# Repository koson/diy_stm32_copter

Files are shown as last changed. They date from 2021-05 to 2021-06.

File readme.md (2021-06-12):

# About the project
- This is my mini project to design a simple PCB that can be used to control a quad or hexa multicopter Design. 
- Thanks PCB Electronics sub-reddit for consulted me.
- The 'stm_multicopter_gerber_v1.2.rar' was used to make the actual PCB I use in this project. -> The bare PCB board photo 'multicopter_bare_pcb.JPG'
- Other notes (mainly plenty of reference PCB design projects): nguye\OneDrive\technical_workspace\Altium_workspace\altium_stm32_copter_hhh
# The firmware
- After finishing soldering the board, I've made several tests on each designed peripherals, you can find them under 'testfirm' folder.
- A video I made to test the ICM AHRS module: https://www.youtube.com/watch?v=TO57MewXJ6E&ab_channel=Edinhthong
- SDcard module code: https://github.com/dinhthong/stm32f4_sd_logger/
# Connect PCB with debugger
## SWD interface
Pin | #Debugger | #Target | #Note
--- | --- | --- | ---
GND | GND | GND 
SWDIO |SWDIO/TMS|JTMS
SWDCLK |SWDCLK/TCK|JTCK
RESET |RESET|NRST |Optional
5V |5V| 5V

Currently The board must connect to power 5V line, GND from 2x3 male header to connect with debugger. The successful connection is shown in the photo. I haven't figured out why this is the case, maybe some problems with my debugging hardware design. Anyway it works :).

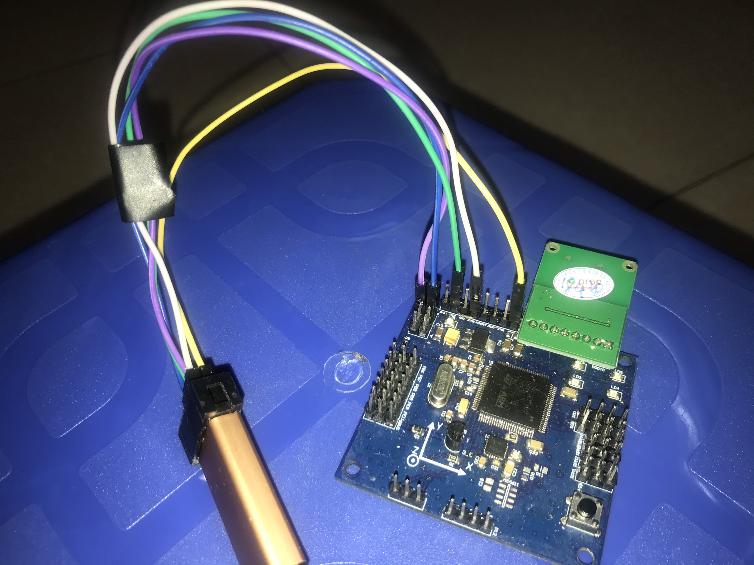
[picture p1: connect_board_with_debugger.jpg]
Debugger Connection

# Todos
## 14 March 2020
- Hàn mạch LM1117, đo điện áp ngõ ra
- Hàn minimal ARM STM32 circuit -> test booting: LED blinking, GPIO PWM, UART.
- Hàn mạch chip IMU: ICM -> test đọc dữ liệu, xin code để đọc mẫu.
## 24 March 2020
- Check các nguồn pin Lipo và sạc nó về 3.85V per cell
- Nối thẳng dây tín hiệu PPM vào đầu input của VĐK, sau đó test code PPM
- Kiếm đầu đọc thẻ nhớ SDIO, lắp vào hàn thử, chạy code
- Test UART thông qua CP2012 cắm vào USB, gửi dữ liệu từ Hercules

# Received papers (from Mr Hoang hardware package)
- Certificate of Origin: Bảng list ra nguồn gốc của linh kiện đã mua.
- Packaging list: tên linh kiện, số lượng order.
- Commercial Invoice: tên linh kiện, số lượng, số tiền tương ứng

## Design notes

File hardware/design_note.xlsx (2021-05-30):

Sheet: todos
 | PWM(TImer1, OC, Timer8, OC) | UART1,2 | mpu9250
đầu vào 5V, có mạch chuyển sang điện áp 3V-3V3 | Timer1 PA8,9,10,11 | PA2,PA3 | loại chân cắm, mục đích để hàn và thay thế dễ
 | Timer8 PC6,7,8,9 | PB6, PB7 | SDI/MOSI, SDO/MISO
 |  | USART3, RX DMA, code dma mình đã thử với USART3 trong quadcopter, nên sẽ chạy đc | cb 9 trục, gyro, accel, mag
chọn con phím nhấn nhỏ gọn, ko như board hiện tại
cần tìm đúng footprint
thiết kế thêm header i2c (software I2C)
chân ADC
lỗ cơ khí các cảm biến như ms5611
ra chân cắm PWM 90 độ như Pixhawk.
consider implementing 4-layer board for better noise reduction?
chân VDDA dùng để làm gì?
chỉ có thắc mắc nên có điện trở ở giữa 2 chân OSCillator hay ko | giá trị ng ta thường dùng là 1M, hoặc là k có gì
ý nghĩa của chân VREF+?, thấy mạch cua rThanh Nhã có design với điện trở 0Ohm @@
Mạch MS5611 cũng rất dễ, nếu sử dụng I2C thì vẽ theo mạch Thanh Nhã, chỉ cần 1 con tụ, và vẽ các chân được config đúng với nhau
vẽ lỗ khoan ngay ở bên mạch schematic??
find footprints for all components
Danh sách linh kiện sử dụng
Cần double check lại mạch schematic, xem xét những chân chưa nối, ra header cho tiện
Cách thay thế con chip ở mạch hiện tại
Tất cả các file sẽ được đưa vào một thư viện chung để dễ kiểm soát
dđi dây mạch mpu9250 thì tham khảo cách chọn linh kiện , wire routing từ project mpu9250 CircuitMaker
còn 1 số chân có NetLabel nhưng chưa ra chân header
layout theo guide của TI cho LM1117, layout MPU9250 theo cái project down được từ CirCuitMaker
2 lớp ở giữa chỉ là phủ đồng nguồn
Thiết kế 2 chân nguồn input 5V, có thể thiết kế 2 cái? | Nếu như tính toán maximum power consumption không đủ
30.1.2020
Tìm kiếm các linh kiện tụ điện, mã sản phẩm, biết được nó dùng chỗ nào trong mạch, sau đó kiếm footprint, và vẽ mạch | cần double-check để confirm 1 lần nữa sau khi đã tìm kiếm tất cả
tham khảo cách xây dựng thư viện riêng cho 1 project của các project mẫu, 3DRobotics,...
31.1.2020
Add các footprint vào schematics và kiểm tra lại
Có 1 số chân chưa kết nối
confirm lại điện trở giữa 2 chân oscillator và điện trở cho sbus để finish
Lớp mạch: Top, Power, Gnd, Bottom
3.2.2020
mcu: 150mA + 5*6.5mA (5 LEDs)
check lai xem ngo ra 3V3, hay la 3V, LM1117
lỗ cố định kích thước M3, ở 4 góc của board | M3 = 126mil=3.2mm
Vẽ hình XYZ của cảm biến, kéo tên các designator để thấy rõ, ghi các chân Power, GND, Signal, + - rõ ràng để cắm mạch | done
Update các linh kiện lên excel sheet online để a Hoàng thấy | done
Thêm các header, jumper vào excelsheet linh kiện | done
5.2.2020
Xử lý các dây Jumper nạp không update qua file PCB, đi lại dây cho mạch, spend about 2 hours | ok done, cần double check lại
mạch nguồn lm1117 tham khảo từ link: https://easyeda.com/layout/5V3_3V_LM1117-0gMGYgasK | mạch 1 lớp, phủ đồng GND
Đặt tên cho các jumper, vẽ hình chiều IMU | done
mạch revo đi 5V như chân bình thường, không đổ polygon nhiều, Vcc thì có pour polygon 1 chút ít ở một lớp
Generally, on a two layer board, both planes are ground
On four layer, it's typically Signal/GND/Power/Signal
Minium Solder Mask Silver Constraint Violation
Silk To Solder Mask Clearance Constraint Violation
Silk To Silk Clearance Constraint Violation
Modified Polygon Violation

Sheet: done
ra chân header cho các pwm
ra chân UART
header để cắm dây oscilloscope debug
VCAP1, VCAP2 ok
need sbus pin's order confirmation for header design
thiết kế thêm chỗ cho Buzzer?? | ko yêu cầu thì khỏi thiết kế nhể
Có nên làm mạch 4 lớp -> người ta thường recommend để cho mạch chạy tốt hơn, nhưng giá cũng mắc tiền hơn
replace stm32f405 with stm32f407 | done
quyết định chọn con LM để làm hạ áp từ 5V->3V | ok
tìm để tham khảo mạch vẽ mpu 9250 | ok
header 2x2 | ok
hỏi về các chân cắm của các cảm biến, external device anh Hoàng
tham khảo mạch mạch power, và hạ áp dùng LM đơn giản của Qflight Controller, Altium Thanh Nhã

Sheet: power
tham khảo mạch nguồn của Thanh Nhã.

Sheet: mechanical, note
chữ trục X,Y ở giữa board, hoặc bên nào đó
các lỗ cơ khí để cố định board

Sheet: footprint
linh kiện, phải kiểm soát từ A-Z, check lại thật kỹ.
để nó ko bị nhầm thì nên ghi thẳng in one of the component's description field in schematic

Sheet: reddit
có nên thêm cuộn dây ở giữa 3V3 và VDDA? Vì thấy trong mạch QCopterFC và Olimex STM32-H405 development board có sử dụng
Bỏ điện trở giữa 2 tụ ở thạch anh ngoại
Không cần điện trở kéo lên/kéo xuống cho cổng SWD

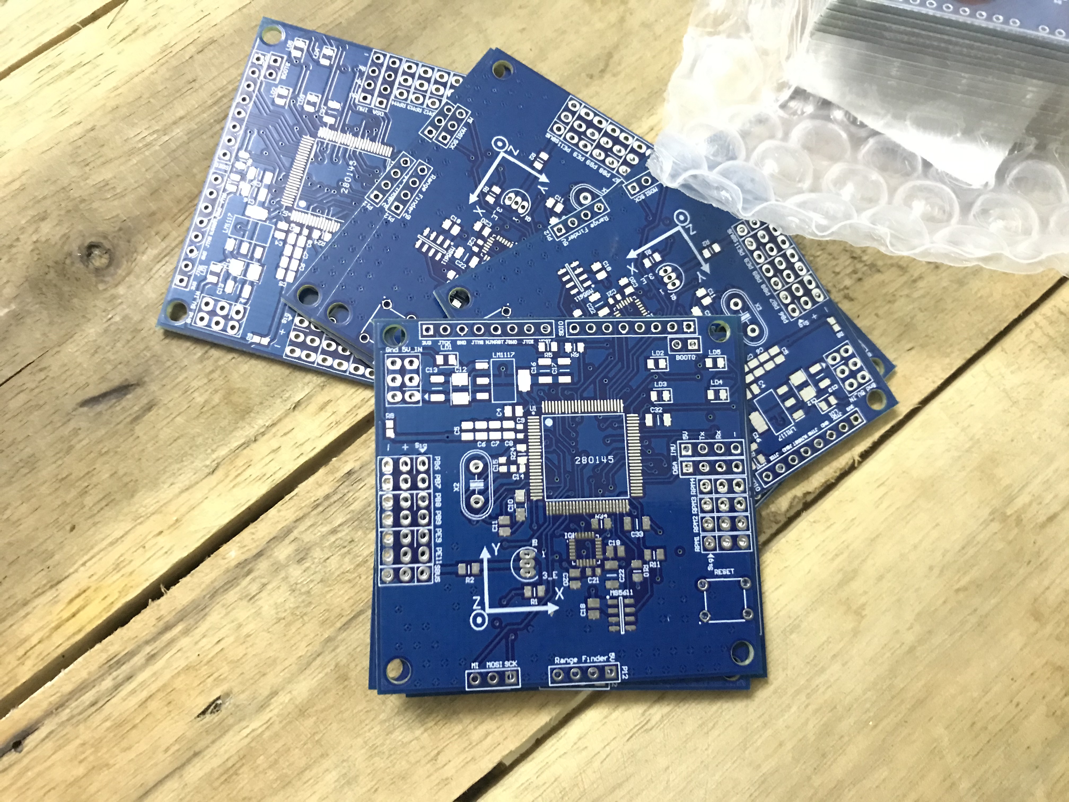
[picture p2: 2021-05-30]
hardware/multicopter_bare_pcb.JPG

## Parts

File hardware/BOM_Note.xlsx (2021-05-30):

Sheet: Next_ver_note
trên maạch drv8323 chỉ có 1 linh kiện gần nhất đó là 30mil, cho nên ở mạch sau cho các linh kiện cách với con chip stm xa ra để dễ hàn hơn | trên mạch của mình hiện tại có nhiều linh kiện quá gần | hiện tại thì hàn cũng k vấn đề gì
Nguồn cắm vào thì nên thiết kế lỗ để hàn dây, đầu jack cắm thì có thể dùng dây của pin Lipo, nhưng như vậy thì có vẻ hơi bất tiện nếu dùng nguồn tổ ong để thử | domino?
đổi switch còn hàng, phù hợp | ok
đổi BJT dán
thiết kế chip SDIO 4-bit | ngay trên mạch, nhưng cần biết thiết kế đi dây đúng mới chạy được
chip stm32f407vgt6 và mạch 4 lớp là thừa cho mạch với yêu cầu hiện tại | có thể nâng cấp thêm một số chức năng để tận dụng tối đa tài nguyên
các header 2.54mm cách đều nhau theo chỉ 1 linh kiện, có thể tự tạo new component theo yêu cầu design của mình
recommend dây cắm như của Pixhawk
bỏ các chân của mạch nạp không cần thiết, chỉ giữ lại 3 chân tín hiệu cần thiết
tham khảo mạch của Revolution Mini và Taulabs Sparky 2
cổng USB OTG để nạp code qua bootloader | not necessary for now, we will load the code via ST-LINK
cầu chì cho mạch điện tử
Note về các header cắm cho next version, và ESD protection circuit.
Các led có thể bố trí lại theo như của Discovery
Đi dây lại nó đẹp và tiết kiệm đường dây hơn, thực tế có thể đi nhiều chân hơn hiện tại, do cách đi của mình là amateur thôi
vẽ footprint cho cụm chân để khỏi sắp xếp từng header gần nhau | xác định trước bao nhiêu chân gần sau nhau đó vẽ footprint 1 thể

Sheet: BOC_v2.5
Item # | Quantity | Designator | Description | Footprint | Link | Component Code | Comment | LibRef
1 | 2 | B2 | Switch | 3-1825910-5 | https://www.mouser.vn/ProductDetail/TE-Connectivity/1825910-1?qs=bdENzIhz2rnt%2FTuoeHeP1Q== | 1825910-1 | SW-PB | SW-PB
2 | 12 | C1, C2, C3, C4, C5, C6, C7, C8, C11, C18, C23 | Capacitor (Semiconductor SIM Model) | CAPC2012X98N | https://www.mouser.vn/ProductDetail/?qs=vLWxofP3U2wSOEpkvhvxCw== | C0805X104K5RAC3316 | 104 | Cap Semi
3 | 1 | C9 | Capacitor (Semiconductor SIM Model) | CAPC1608X90N | https://www.mouser.vn/ProductDetail/Yageo/CC0603KRX5R7BB105?qs=GgnqJ2f3nHgfglcojISamw== | CC0603KRX5R7BB105 | 1uF | Cap Semi
4 | 1 | C10 | Polarized Capacitor (Axial) | CAPPM3216X180N | https://www.mouser.com/ProductDetail/AVX/TAJA105K016RNJ?qs=sGAEpiMZZMuEN2agSAc2pmRv4r8cj6yF/yQO0PAbRXc= | TAJA105K016RNJ | 1uF | Cap Pol2
5 | 1 | C12 | Tantalum Capacitor | CAPPM3528X210N | https://www.mouser.vn/ProductDetail/AVX/TAJB106K016RSJ?qs=wgedUHV26DXCOqbRtdjeKQ== | TAJB106K016RSJ | 10uF | Cap_Tan_1210
6 | 3 | C13, C16, C17 | Capacitor | CAPC3216X135N | https://www.mouser.vn/ProductDetail/KEMET/C1206C104J5JACTU | C1206C104J5JACTU | Cap_0603 | Cap_0603
7 | 2 | C14, C15 | Capacitor (Semiconductor SIM Model) | CAPC1608X95N | https://www.mouser.vn/ProductDetail/KEMET/C0603C220J5GAC7411 | C0603C220J5GAC7411 | 22pF | Cap Semi
8 | 1 | C19 | Capacitor (Semiconductor SIM Model) | CAPC2012X145N | https://www.mouser.vn/ProductDetail/Vishay-Vitramon/VJ0805Y104KNAAT | VJ0805Y104KNAAT | 0.1uF | Cap Semi
9 | 1 | C20 | Capacitor (Semiconductor SIM Model) | CAPC2012X145N | https://www.mouser.vn/ProductDetail/Vishay-Vitramon/VJ0805Y103KNAAO | VJ0805Y103KNAAO | 10nF | Cap Semi
10 | 3 | C32, C33, C22 | Capacitor (Semiconductor SIM Model) | CAPC3216X125N | https://www.mouser.vn/ProductDetail/Yageo/CC1206KKX7R7BB225 | CC1206KKX7R7BB225 | 2.2uF | Cap Semi
11 | 1 | C21 |  | CAPC1608X90N | https://www.mouser.vn/ProductDetail/Yageo/CC0603KRX7R8BB474?qs=sGAEpiMZZMs0AnBnWHyRQJ8ZYmg6NYZbMHOVgCI8LDs%3D | CC0603KRX7R8BB474 | 0.47uF
12 | 1 | IC1 | Integrated Circuit | SOT230P700X180-4N | https://www.mouser.vn/ProductDetail/Texas-Instruments/LM1117IMPX-33-NOPB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 | LM1117IMPX3.3_NOPB | LM1117IMPX3.3_NOPB | LM1117IMPX3.3_NOPB
13 | 1 | IC2 | Integrated Circuit | SON125P300X500X100-8N | https://www.mouser.vn/ProductDetail/Measurement-Specialties/MS561101BA03-50 | MS561101BA03-50 | MS561101BA03-00 | MS561101BA03-00
14 | 2 | LD1, LD2 | LED_RED | LEDC2012X120N | https://www.mouser.vn/ProductDetail/Lite-On/LTST-C170KRKT | LTST-C170KRKT | LTST-C171GKT | LTST-C171GKT
15 | 1 | LD3 | LED_GREEN | LEDC2012X90N | https://www.mouser.vn/ProductDetail/Lite-On/LTST-C171GKT | LTST-C171GKT
16 | 1 | LD4 | LED_BLUE | LEDC2012X90N | https://www.mouser.vn/ProductDetail/Lite-On/LTST-C171TBKT | LTST-C171TBKT
17 | 1 | LD5 | LED_YELLOW | LEDC2012X120N | https://www.mouser.vn/ProductDetail/Lite-On/LTST-C170YKT | LTST-C170YKT
18 | 1 | Q1 | NPN Darlington Bipolar Transistor | TO-92 | https://banlinhkien.vn/goods-1920-s9014-to-92.html |  | NPN1 | NPN1
19 | 13 | R1, R3, R4, R5, R6, R7, R9, R13, R24, R34, R10, R11 | Resistor | RESC2012X60N | https://www.mouser.vn/ProductDetail/Yageo/SR0805FR-7T10KL?qs=pfd5qewlna5WQnzPK%252BoHUA== | RC0805FR-0710KL | 10K | Res3
20 | 1 | R2 | Resistor | RESC2012X60N | https://www.mouser.vn/ProductDetail/Yageo/RC0805FR-071KL?qs=1ogmaHw32WJjeGY0DHXakQ== | RC0805FR-071KL | 1K | Res3
21 | 5 | R8, R14, R15, R16, R17 | Resistor | RESC1608X55N | https://www.mouser.vn/ProductDetail/Yageo/RC0603FR-07510RL?qs=gt6vzsuosg04lV7mPQHzdw== | RC0603FR-07510RL |  | Res3
22 | 1 | U1 | ARM Cortex-M4 32-bit MCU+FPU, 210 DMIPS, 1024 kB Flash, 192 kB Internal RAM, 82 I/Os, 100-pin LQFP, -40 to 85 degC, Tray | STM-LQFP100_N | https://banlinhkien.vn/goods-3297-stm32f407vgt6-lqfp100.html |  | STM32F407VGT6 | STM32F407VGT6
23 | 1 | IC1 |  | ICM20689 | https://www.mouser.vn/ProductDetail/TDK-InvenSense/ICM-20689 | ICM-20689 | ICM-20689 | ICM-20689
24 | 1 | X2 | Crystal For all Crystal 2pin. | XT2 | https://banlinhkien.vn/goods-779-thach-anh-8mhz-49s-dip.html |  | 8Mhz | XT2
26 | 2 |  | 40 pin male header strip | cần 52 chân | https://hshop.vn/products/rao-duc-don-chon-thang-dai-40chon
27 | 1 |  | 90 degree header | cần 7x3 chân | https://www.adafruit.com/product/816

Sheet: BOC_v2.6
Item # | Quantity | Designator | Description | Footprint | Link | Component Code | Comment | LibRef | Mouser Received Quantity |  |  | USD price | Price per board
1 | 2 | B2 | Switch | 3-1825910-5 | https://www.mouser.vn/ProductDetail/TE-Connectivity/1825910-1?qs=bdENzIhz2rnt%2FTuoeHeP1Q== | 1825910-1 | SW-PB | SW-PB
2 | 12 | C1, C2, C3, C4, C5, C6, C7, C8, C11, C18, C23 | Capacitor (Semiconductor SIM Model) | CAPC2012X98N | https://www.mouser.vn/ProductDetail/?qs=vLWxofP3U2wSOEpkvhvxCw== | C0805X104K5RAC3316 | 104 | Cap Semi | 50 | OK |  | 9.7 | 2.328
3 | 1 | C9 | Capacitor (Semiconductor SIM Model) | CAPC1608X90N | https://www.mouser.vn/ProductDetail/Yageo/CC0603KRX5R7BB105?qs=GgnqJ2f3nHgfglcojISamw== | CC0603KRX5R7BB105 | 1uF | Cap Semi | 10 | OK |  | 0.91 | 0.091
4 | 1 | C10 | Polarized Capacitor (Axial) | CAPPM3216X180N | https://www.mouser.com/ProductDetail/AVX/TAJA105K016RNJ?qs=sGAEpiMZZMuEN2agSAc2pmRv4r8cj6yF/yQO0PAbRXc= | TAJA105K016RNJ | 1uF | Cap Polarity | 10 |  | Dark size is +. https://electronics.stackexchange.com/questions/35480/polarity-of-unmarked-smt-electrolytic-capacitor | 2.16 | 0.216
5 | 1 | C12 | Tantalum Capacitor | CAPPM3528X210N | https://www.mouser.vn/ProductDetail/AVX/TAJB106K016RSJ?qs=wgedUHV26DXCOqbRtdjeKQ== | TAJB106K016RSJ | 10uF | Cap_Tantalum, polarized | 10 |  |  | 3 | 0.3
6 | 3 | C13, C16, C17 | Capacitor | CAPC3216X135N | https://www.mouser.vn/ProductDetail/KEMET/C1206C104J5JACTU | C1206C104J5JACTU | Cap_0603 | Cap_0603 | 10 |  |  | 5.79 | 1.737
7 | 2 | C14, C15 | Capacitor (Semiconductor SIM Model) | CAPC1608X95N | https://www.mouser.vn/ProductDetail/KEMET/C0603C220J5GAC7411 | C0603C220J5GAC7411 | 22pF | Cap Semi | 10 |  |  | 1.03 | 0.206
8 | 1 | C19 | Capacitor (Semiconductor SIM Model) | CAPC2012X145N | https://www.mouser.vn/ProductDetail/Vishay-Vitramon/VJ0805Y104KNAAT | VJ0805Y104KNAAT | 0.1uF | Cap Semi | 10 |  |  | 5.9 | 0.59
9 | 1 | C20 | Capacitor (Semiconductor SIM Model) | CAPC2012X145N | https://www.mouser.vn/ProductDetail/Vishay-Vitramon/VJ0805Y103KNAAO | VJ0805Y103KNAAO | 10nF | Cap Semi | 10 | ok |  | 5.4 | 0.54
10 | 3 | C32, C33, C22 | Capacitor (Semiconductor SIM Model) | CAPC3216X125N | https://www.mouser.vn/ProductDetail/Yageo/CC1206KKX7R7BB225 | CC1206KKX7R7BB225 | 2.2uF | Cap Semi | 10 |  |  | 2.55 | 0.765
11 | 1 | C21 |  | CAPC1608X90N | https://www.mouser.vn/ProductDetail/Yageo/CC0603KRX7R8BB474?qs=sGAEpiMZZMs0AnBnWHyRQJ8ZYmg6NYZbMHOVgCI8LDs%3D | CC0603KRX7R8BB474 | 0.47uF |  | 10 |  |  | 0.87 | 0.087
12 | 1 | IC1 | Integrated Circuit | SOT230P700X180-4N | https://www.mouser.vn/ProductDetail/Texas-Instruments/LM1117IMPX-33-NOPB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 | LM1117IMPX3.3_NOPB | LM1117IMPX3.3_NOPB | LM1117IMPX3.3_NOPB | 10 | ok |  | 9.4 | 0.94
13 | 1 | IC2 | Integrated Circuit | SON125P300X500X100-8N | https://www.mouser.vn/ProductDetail/Measurement-Specialties/MS561101BA03-50 | MS561101BA03-50 | MS561101BA03-00 | MS561101BA03-00 | 1 |  |  | x
14 | 2 | LD1, LD2 | LED_RED | LEDC2012X120N | https://www.mouser.vn/ProductDetail/Lite-On/LTST-C170KRKT | LTST-C170KRKT | LTST-C171GKT | LTST-C171GKT | 10 |  |  | 1.7 | 0.34
15 | 1 | LD3 | LED_GREEN | LEDC2012X90N | https://www.mouser.vn/ProductDetail/Lite-On/LTST-C171GKT | LTST-C171GKT |  |  | 10 |  |  | 1.4 | 0.14
16 | 1 | LD4 | LED_BLUE | LEDC2012X90N | https://www.mouser.vn/ProductDetail/Lite-On/LTST-C171TBKT | LTST-C171TBKT |  |  | 10 |  |  | 2.5 | 0.25
17 | 1 | LD5 | LED_YELLOW | LEDC2012X120N | https://www.mouser.vn/ProductDetail/Lite-On/LTST-C170YKT | LTST-C170YKT |  |  | 10 |  |  | 1.8 | 0.18
18 | 1 | Q1 | NPN Darlington Bipolar Transistor | TO-92 | https://banlinhkien.vn/goods-1920-s9014-to-92.html |  | NPN1 | NPN1 | 10
19 | 13 | R1, R3, R4, R5, R6, R7, R9, R13, R24, R34, R10, R11 | Resistor | RESC2012X60N | https://www.mouser.vn/ProductDetail/Yageo/SR0805FR-7T10KL?qs=pfd5qewlna5WQnzPK%252BoHUA== | RC0805FR-0710KL | 10K | Res3 | 60 |  |  |  | 0.611
20 | 1 | R2 | Resistor | RESC2012X60N | https://www.mouser.vn/ProductDetail/Yageo/RC0805FR-071KL?qs=1ogmaHw32WJjeGY0DHXakQ== | RC0805FR-071KL | 1K | Res3 | 10 |  |  | 0.31 | 0.031
21 | 5 | R8, R14, R15, R16, R17 | Resistor | RESC1608X55N | https://www.mouser.vn/ProductDetail/Yageo/RC0603FR-07510RL?qs=gt6vzsuosg04lV7mPQHzdw== | RC0603FR-07510RL |  | Res3 | 20 | ok |  | 0.36 | 0.09
22 | 1 | U1 | ARM Cortex-M4 32-bit MCU+FPU, 210 DMIPS, 1024 kB Flash, 192 kB Internal RAM, 82 I/Os, 100-pin LQFP, -40 to 85 degC, Tray | STM-LQFP100_N | https://banlinhkien.vn/goods-3297-stm32f407vgt6-lqfp100.html |  | STM32F407VGT6 | STM32F407VGT6 | 5 | ok |  | 58.55 | 11.71
23 | 1 | IC1 |  | ICM20689 | https://www.mouser.vn/ProductDetail/TDK-InvenSense/ICM-20689 | ICM-20689 | ICM-20689 | ICM-20689 | 10 | ok |  | 39 | 3.9
24 | 1 | X2 | Crystal For all Crystal 2pin. | XT2 | https://banlinhkien.vn/goods-779-thach-anh-8mhz-49s-dip.html |  | 8Mhz | XT2 | 5 | ok |  | 2.5 | 0.5
26 | 2 |  | 40 pin male header strip | cần 52 chân | https://hshop.vn/products/rao-duc-don-chon-thang-dai-40chon
27 | 1 |  | 90 degree header | cần 7x3 chân | https://www.adafruit.com/product/816
 |  |  |  |  |  |  |  |  |  |  |  |  | 25.552

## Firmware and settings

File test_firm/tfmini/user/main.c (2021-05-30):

#include "stm32f4xx.h"
#include "stm32f4xx_it.h"
#include "string.h"
/*
https://stm32f4-discovery.net/2017/07/stm32-tutorial-efficiently-receive-uart-data-using-dma/
GPS STM32 for quadcopter.
*/
void tfmini_init(void);
void tfmini_parsing(void);

void delay_us(uint32_t period){
	
  	RCC_APB1PeriphClockCmd(RCC_APB1Periph_TIM2, ENABLE);
  	TIM2->PSC = 83;		// clk = SystemCoreClock /2/(PSC+1) = 1MHz
  	TIM2->ARR = period-1;
  	TIM2->CNT = 0;
  	TIM2->EGR = 1;		// update registers;
  	TIM2->SR  = 0;		// clear overflow flag
  	TIM2->CR1 = 1;		// enable Timer6
  	while (!TIM2->SR);
  	TIM6->CR2 = 0;		// stop Timer6
  	RCC_APB1PeriphClockCmd(RCC_APB1Periph_TIM2, DISABLE);
}
//delay 0.1ms
void delay_01ms(uint16_t period){
	
  	RCC_APB1PeriphClockCmd(RCC_APB1Periph_TIM6, ENABLE);
  	TIM6->PSC = 8399;		// clk = SystemCoreClock /2 /(PSC+1) = 10KHz
  	TIM6->ARR = period-1;
  	TIM6->CNT = 0;
  	TIM6->EGR = 1;		// update registers;
  	TIM6->SR  = 0;		// clear overflow flag
  	TIM6->CR1 = 1;		// enable Timer6
  	while (!TIM6->SR);
  	TIM6->CR1 = 0;		// stop Timer6
  	RCC_APB1PeriphClockCmd(RCC_APB1Periph_TIM6, DISABLE);
}

/* Receive buffer for DMA */
// 725
#define DMA_RX_BUFFER_SIZE          50
uint8_t DMA_RX_Buffer[DMA_RX_BUFFER_SIZE];
DMA_InitTypeDef DMA_InitStruct;
NVIC_InitTypeDef NVIC_InitStruct;
GPIO_InitTypeDef  GPIO_InitStructure;
GPIO_InitTypeDef GPIO_InitStruct;
USART_InitTypeDef USART_InitStruct;
NVIC_InitTypeDef NVIC_InitStructure;
uint16_t tfmini_distance, tfmini_strength;
int main(void)
{
		RCC->AHB1ENR |= RCC_AHB1Periph_GPIOD;
	
		/* Configure PD12, PD13 in output pushpull mode */
		GPIO_InitStructure.GPIO_Pin = GPIO_Pin_12|GPIO_Pin_13|GPIO_Pin_14|GPIO_Pin_15 ;
		GPIO_InitStructure.GPIO_Mode = GPIO_Mode_OUT;
		GPIO_InitStructure.GPIO_OType = GPIO_OType_PP;
		GPIO_InitStructure.GPIO_Speed = GPIO_Speed_100MHz;
		GPIO_InitStructure.GPIO_PuPd = GPIO_PuPd_NOPULL;
		GPIO_Init(GPIOD, &GPIO_InitStructure);
	  tfmini_init();
	
  while (1)
  {

  }
}
//2 ways
void UARTmain_Init()
{
 
}
void USART3_IRQHandler(void)
{
	  if (USART3->SR & USART_FLAG_IDLE) {         /* We want IDLE flag only */
        DMA_Cmd(DMA1_Stream1, DISABLE);
        /* This part is important */
        /* Clear IDLE flag by reading status register first */
        /* And follow by reading data register */
        volatile uint32_t tmp;                  /* Must be volatile to prevent optimizations */
        tmp = USART3->SR;                       /* Read status register */
        tmp = USART3->DR;                       /* Read data register */
      //  DMA1_Stream1->CR &= ~DMA_SxCR_EN;       /* Disabling DMA will force transfer complete interrupt if enabled */
		//	  idle_cnt++;
					//	DMA_Cmd(DMA1_Stream1, DISABLE);
      
		//	DMA1->HIFCR = DMA_FLAG_DMEIF1 | DMA_FLAG_FEIF1 | DMA_FLAG_HTIF1 | DMA_FLAG_TCIF1 | DMA_FLAG_TEIF1;
	//		DMA_Init(DMA1_Stream1, &DMA_InitStruct);
			
				DMA1_Stream1->M0AR = (uint32_t)DMA_RX_Buffer;   /* Set memory address for DMA again */
        DMA1_Stream1->NDTR = DMA_RX_BUFFER_SIZE;    /* Set number of bytes to receive */
			  DMA_Cmd(DMA1_Stream1, ENABLE);
	//		  DMA1_Stream1->M0AR = (uint32_t)DMA_RX_Buffer;   /* Set memory address for DMA again */
	     tfmini_parsing();
			  
    }	
}

void tfmini_parsing(void) {
	int m;
	if (DMA_RX_Buffer[0]==0x59) {
		tfmini_distance = (DMA_RX_Buffer[3]>>8)+DMA_RX_Buffer[2];
		tfmini_strength = (DMA_RX_Buffer[5]>>8)+DMA_RX_Buffer[4];
	}
	}


void tfmini_init(void) {
	uint8_t kk;
	  RCC_APB1PeriphClockCmd(RCC_APB1Periph_USART3, ENABLE);
    RCC_AHB1PeriphClockCmd(RCC_AHB1Periph_GPIOB, ENABLE);
	  RCC_AHB1PeriphClockCmd(RCC_AHB1Periph_DMA1, ENABLE);
	
    GPIO_InitStruct.GPIO_Mode = GPIO_Mode_AF;
    GPIO_InitStruct.GPIO_Pin = GPIO_Pin_10 | GPIO_Pin_11;
    GPIO_InitStruct.GPIO_Speed = GPIO_Speed_100MHz;
    GPIO_InitStruct.GPIO_OType = GPIO_OType_PP;
    GPIO_InitStruct.GPIO_PuPd = GPIO_PuPd_UP;
    GPIO_Init(GPIOB, &GPIO_InitStruct);
	
	  /*PD5 to PL2303 RX*/
    GPIO_PinAFConfig(GPIOB, GPIO_PinSource10, GPIO_AF_USART3);//UART Tx pins 
    GPIO_PinAFConfig(GPIOB, GPIO_PinSource11, GPIO_AF_USART3);//UART Rx pins
	
    //USART2 configuration
    USART_InitStruct.USART_BaudRate = 115200;
    USART_InitStruct.USART_HardwareFlowControl = USART_HardwareFlowControl_None;
    USART_InitStruct.USART_Mode = USART_Mode_Tx|USART_Mode_Rx;
    USART_InitStruct.USART_Parity = USART_Parity_No;
    USART_InitStruct.USART_StopBits = USART_StopBits_1;
    USART_InitStruct.USART_WordLength = USART_WordLength_8b;
    USART_Init(USART3, &USART_InitStruct);
		
		NVIC_InitStructure.NVIC_IRQChannel = USART3_IRQn;
		NVIC_InitStructure.NVIC_IRQChannelPreemptionPriority = 0;
		NVIC_InitStructure.NVIC_IRQChannelSubPriority = 0;
		NVIC_InitStructure.NVIC_IRQChannelCmd = ENABLE;
		NVIC_Init(&NVIC_InitStructure);
//		USART_ITConfig(USART3, USART_IT_RXNE, ENABLE);
		USART_ITConfig(USART3, USART_IT_IDLE, ENABLE);
		USART_Cmd(USART3, ENABLE);
	  USART_DMACmd(USART3, USART_DMAReq_Rx, ENABLE);
	
	  /* Configure DMA for USART RX, DMA1, Stream1, Channel4 */
    DMA_StructInit(&DMA_InitStruct);
    DMA_InitStruct.DMA_Channel = DMA_Channel_4;
    DMA_InitStruct.DMA_Memory0BaseAddr = (uint32_t)DMA_RX_Buffer;
    DMA_InitStruct.DMA_BufferSize = DMA_RX_BUFFER_SIZE;
    DMA_InitStruct.DMA_PeripheralBaseAddr = (uint32_t)&USART3->DR;
    DMA_InitStruct.DMA_DIR = DMA_DIR_PeripheralToMemory;
    DMA_InitStruct.DMA_MemoryDataSize = DMA_MemoryDataSize_Byte;
    DMA_InitStruct.DMA_PeripheralDataSize = DMA_PeripheralDataSize_Byte;
		DMA_InitStruct.DMA_Mode = DMA_Mode_Circular;
		DMA_InitStruct.DMA_Priority = DMA_Priority_High;
    DMA_InitStruct.DMA_MemoryInc = DMA_MemoryInc_Enable;
    DMA_InitStruct.DMA_PeripheralInc = DMA_PeripheralInc_Disable;
    DMA_Init(DMA1_Stream1, &DMA_InitStruct);
		DMA_Cmd(DMA1_Stream1, ENABLE);
// send setting
uint8_t command[] = {0x42, 0x57,0x02,0x00,0x00,0x00,0x01,0x06};
			for (kk=0;kk<8;kk++) {
			while(USART_GetFlagStatus(USART3, USART_FLAG_TXE) == RESET) {
				USART_SendData(USART3,command[kk]);
			}
			}
}

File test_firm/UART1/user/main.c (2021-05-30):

#include "stm32f4xx.h"
#include "stm32f4xx_it.h"
/*
Demonstrate how to implement 'C printf() function' to transfer USART
The buffer for receipt must be determined. Or else must change the code appropriately for correct use.
*/
#define BUFFERSIZE 5
void UARTmain_Init(void);
int i;
void Delay(int t){
	int i;
	for (i=0; i<t; i++);
}

void delay_us(uint32_t period){
  	RCC_APB1PeriphClockCmd(RCC_APB1Periph_TIM2, ENABLE);
  	TIM2->PSC = 83;		// clk = SystemCoreClock /2/(PSC+1) = 1MHz
  	TIM2->ARR = period-1;
  	TIM2->CNT = 0;
  	TIM2->EGR = 1;		// update registers;
  	TIM2->SR  = 0;		// clear overflow flag
  	TIM2->CR1 = 1;		// enable Timer6
  	while (!TIM2->SR);
  	TIM6->CR2 = 0;		// stop Timer6
  	RCC_APB1PeriphClockCmd(RCC_APB1Periph_TIM2, DISABLE);
}
//delay 0.1ms
void delay_01ms(uint16_t period){
	
  	RCC_APB1PeriphClockCmd(RCC_APB1Periph_TIM6, ENABLE);
  	TIM6->PSC = 8399;		// clk = SystemCoreClock /2 /(PSC+1) = 10KHz
  	TIM6->ARR = period-1;
  	TIM6->CNT = 0;
  	TIM6->EGR = 1;		// update registers;
  	TIM6->SR  = 0;		// clear overflow flag
  	TIM6->CR1 = 1;		// enable Timer6
  	while (!TIM6->SR);
  	TIM6->CR1 = 0;		// stop Timer6
  	RCC_APB1PeriphClockCmd(RCC_APB1Periph_TIM6, DISABLE);
}
char RxBuffer[BUFFERSIZE];
__IO uint8_t RxIndex = 0x00;
uint8_t count;
int main(void)
{
  	GPIO_InitTypeDef  GPIO_InitStructure;
  	/* GPIOD Peripheral clock enable */
 	// RCC_AHB1PeriphClockCmd(RCC_AHB1Periph_GPIOD, ENABLE);
	RCC->AHB1ENR |= RCC_AHB1Periph_GPIOD;
	/* Configure PD12, PD13 in output pushpull mode */
	GPIO_InitStructure.GPIO_Pin = GPIO_Pin_12|GPIO_Pin_13|GPIO_Pin_14|GPIO_Pin_15 ;
	GPIO_InitStructure.GPIO_Mode = GPIO_Mode_OUT;
	GPIO_InitStructure.GPIO_OType = GPIO_OType_PP;
	GPIO_InitStructure.GPIO_Speed = GPIO_Speed_100MHz;
	GPIO_InitStructure.GPIO_PuPd = GPIO_PuPd_NOPULL;
	GPIO_Init(GPIOD, &GPIO_InitStructure);
	UARTmain_Init();
  while (1)
  {
		//count++;
		delay_01ms(500);
		printf("Hello world %d\r\n", count);
		count++;
   		// GPIO_SetBits(GPIOD,GPIO_Pin_12|GPIO_Pin_13|GPIO_Pin_14|GPIO_Pin_15);
		GPIOD->BSRRL = GPIO_Pin_12|GPIO_Pin_13|GPIO_Pin_14|GPIO_Pin_15;
		delay_01ms(500);
		//GPIO_ResetBits(GPIOD,GPIO_Pin_12|GPIO_Pin_13|GPIO_Pin_14|GPIO_Pin_15);
		GPIOD->BSRRH = GPIO_Pin_12|GPIO_Pin_13|GPIO_Pin_14|GPIO_Pin_15;
  }
}
//2 ways
void UARTmain_Init()
{
	GPIO_InitTypeDef GPIO_InitStruct;
    USART_InitTypeDef USART_InitStruct;
	NVIC_InitTypeDef NVIC_InitStructure;
	
	RCC_APB2PeriphClockCmd(RCC_APB2Periph_USART1, ENABLE);
    RCC_AHB1PeriphClockCmd(RCC_AHB1Periph_GPIOA, ENABLE);
	
    GPIO_InitStruct.GPIO_Mode=GPIO_Mode_AF;
    GPIO_InitStruct.GPIO_Pin=GPIO_Pin_9|GPIO_Pin_10;
    GPIO_InitStruct.GPIO_Speed=GPIO_Speed_100MHz;
    GPIO_InitStruct.GPIO_OType=GPIO_OType_PP;
    GPIO_InitStruct.GPIO_PuPd=GPIO_PuPd_UP;
    GPIO_Init(GPIOA, &GPIO_InitStruct);
	
	/*PD5 to PL2303 RX*/
    GPIO_PinAFConfig(GPIOA, GPIO_PinSource9, GPIO_AF_USART1);//UART Tx pins 
    GPIO_PinAFConfig(GPIOA, GPIO_PinSource10, GPIO_AF_USART1);//UART Rx pins
	
    //USART1 configuration
    USART_InitStruct.USART_BaudRate=115200;
    USART_InitStruct.USART_HardwareFlowControl=USART_HardwareFlowControl_None;
    USART_InitStruct.USART_Mode=USART_Mode_Tx|USART_Mode_Rx;
    USART_InitStruct.USART_Parity=USART_Parity_No;
    USART_InitStruct.USART_StopBits=USART_StopBits_1;
    USART_InitStruct.USART_WordLength=USART_WordLength_8b;
    USART_Init(USART1, &USART_InitStruct);
		
	NVIC_InitStructure.NVIC_IRQChannel = USART1_IRQn;
	NVIC_InitStructure.NVIC_IRQChannelPreemptionPriority = 1;
	NVIC_InitStructure.NVIC_IRQChannelSubPriority = 1;
	NVIC_InitStructure.NVIC_IRQChannelCmd = ENABLE;
	NVIC_Init(&NVIC_InitStructure);
	USART_ITConfig(USART1, USART_IT_RXNE, ENABLE);
	USART_Cmd(USART1, ENABLE);  
}
void USART1_IRQHandler(void)
{
	// Transfer interrupt
    if (USART_GetITStatus(USART1, USART_IT_TXE) != RESET) {
    }
    // Receive interrupt
    if (USART_GetITStatus(USART1, USART_IT_RXNE) != RESET) {
    //read from USART_DR will automatically clear the RNXE bit.
	if (RxIndex >= BUFFERSIZE)
    {
			RxIndex=0;
    /* Receive Transaction data */
    }
		RxBuffer[RxIndex++] = USART_ReceiveData(USART1);
	}
}

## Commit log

2021-05-30 Organize all things of this project -> upload to github
    [BOM_Note.xlsx, Pinout.SchDoc, SENSORS.SchDoc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]
2021-05-30 update notes (reference projects on my OneDrive)
    [design_note.xlsx]
2021-06-12 add connect the board with debugger
